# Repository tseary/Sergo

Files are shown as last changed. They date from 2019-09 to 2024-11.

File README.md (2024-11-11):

# Sergo
Sergo is a custom circuit board I made to interface hobby servos (or Geek servos) with Lego Power Functions. It has an ATTINY84 microcontroller and a 5 V, 2.5 A buck converter. It supports up to two servos, and can be controlled either from a PF receiver or directly by IR remote. It is programmed in Arduino.

54124418031_3b0a96d11d_c

# Make Your Own
Disclaimer: This is not a how-to guide. I have shared this project for general interest and in case the source code is useful to anyone. However, if you want to make your own Sergo, I am assuming you already have some knowledge of surface-mount soldering. You will need reflow soldering materials and equipment. **This project _cannot_ be assembled with only a soldering iron!**

## Gather Parts
The bare PCB without components can be ordered from [OSH Park](https://oshpark.com/shared_projects/rSyxp330).



Here is a [Digikey cart](https://www.digikey.ca/short/tn3525p4) with all of the components. The cost of parts for one board is about $15.61 CAD (or $13.92 CAD if the IR receiver is omitted).

It is recommended to apply solder paste to the board with a stencil. I used a polyimide film stencil of 0.005" thickness from [OSH Stencils](https://www.oshstencils.com). The stencil gerber file is "KiCad/gerbers/Sergo-F_Paste.gbr". Alternatively, solder paste may be applied freehand with a syringe. Particular care should be taken to apply the paste neatly under the buck converter PS1.

## Assembly, Programming, and Testing
More details to come...

# Show Me!
If you do attempt to build this project, I'd like to see it! Find me on [Eurobricks](https://www.eurobricks.com/forum/index.php?/profile/207750-tseary/).

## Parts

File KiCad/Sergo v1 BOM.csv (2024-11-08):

Id | Designator | Package | Quantity | Designation | Supplier and ref
1 | C1 | 1206 | 1 | 47uF
2 | C4,C5,C3 | 0805 | 3 | 0.1uF
3 | P2 | Pin_Header_02x03 | 1 | ICSP
4 | P3 | Pin_Header_02x03 | 1 | SERVOS
5 | U2 | TSOP382_RA | 1 | TSOP38238
6 | C2 | C_SMT_D8 | 1 | 220uF 10V
7 | R2,R3 | 0805 | 2 | 10k
8 | R4 | 0805 | 1 | 33
9 | PS1 | DC-DC_MYLSM00502ERPL | 1 | MYLSM00502ERPL
10 | P1 | Conn_Micro-MaTch_215570-4 | 1 | POWER FUNCTIONS
11 | F1 | 1812 | 1 | 1.5A
12 | D1 | SOT-23_Diode_ANK | 1 | 15V
13 | D2 | SOT-23 | 1 | ZENER 4.3V
14 | U1 | SOIC-14 | 1 | ATTINY84-S
15 | R1 | 0805 | 1 | 1k
16 | JP2 | 0805_JUMPER | 1 | CH2
17 | JP1 | 0805_JUMPER | 1 | CH1

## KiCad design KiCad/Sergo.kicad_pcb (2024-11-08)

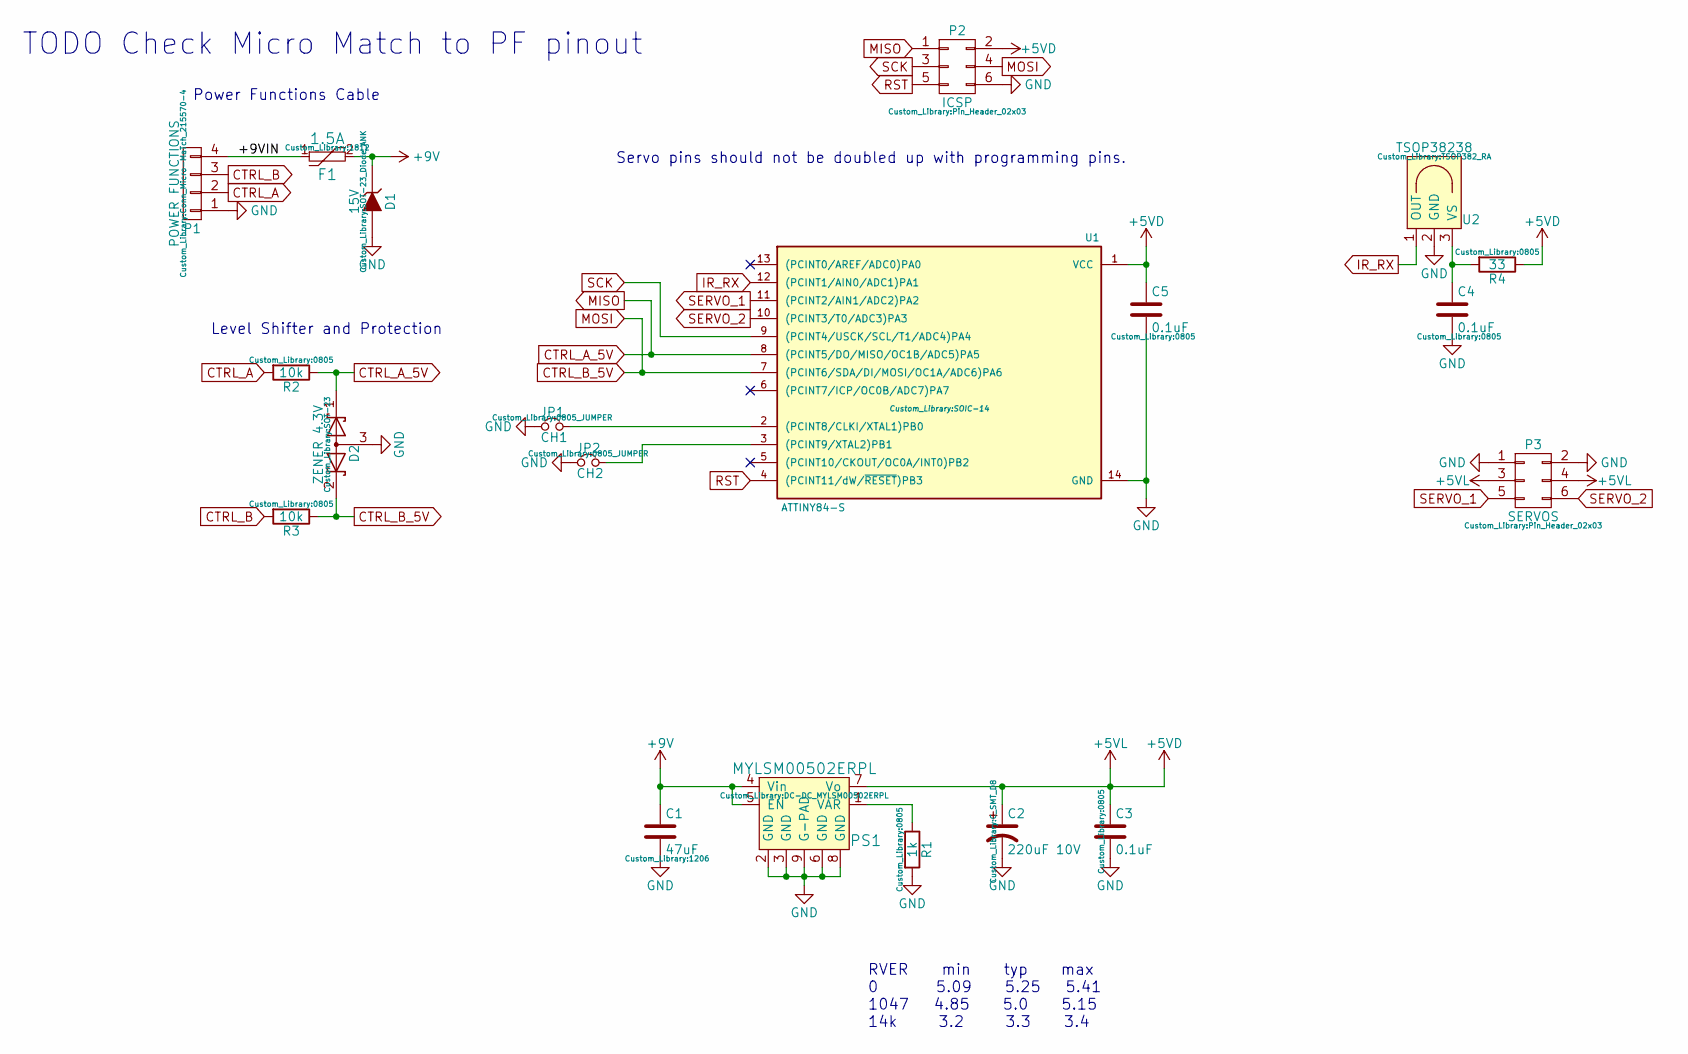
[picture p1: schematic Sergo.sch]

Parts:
C1: 47uF; 1206
C2: 220uF 10V; C_SMT_D8
C3, C4, C5: 0.1uF; 0805
D1: 15V; SOT-23_Diode_ANK
D2: ZENER 4.3V; SOT-23
F1: 1.5A; 1812
JP1: CH1; 0805_JUMPER
JP2: CH2; 0805_JUMPER
P1: POWER FUNCTIONS; Conn_Micro-MaTch_215570-4
P2: ICSP; Pin_Header_02x03
P3: SERVOS; Pin_Header_02x03
PS1: MYLSM00502ERPL; DC-DC_MYLSM00502ERPL
R1: 1k; 0805
R2, R3: 10k; 0805
R4: 33; 0805
U1: ATTINY84-S; SOIC-14
U2: TSOP38238; TSOP382_RA

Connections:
+5VD: C2.1, C3.1, C5.1, P2.2, P3.3, P3.4, PS1.7 (Vo), R4.1, U1.1 (VCC)
+9V: C1.1, D1.1 (K), F1.2, PS1.4 (Vin), PS1.5 (EN)
/+9VIN: F1.1, P1.4
CTRL_A: P1.2, R2.2
CTRL_B: P1.3, R3.2
CTRL_B_5V: D2.2 (K), P2.4, R3.1, U1.7 ((PCINT6/SDA/DI/MOSI/OC1A/ADC6)PA6)
GND: C1.2, C2.2, C3.2, C4.2, C5.2, D1.2 (A), D2.3 (A), JP1.1, JP2.1, P1.1, P2.6, P3.1, P3.2, PS1.2 (GND), PS1.3 (GND), PS1.6 (GND), PS1.8 (GND), PS1.9 (G-PAD), R1.2, U1.14 (GND), U2.2 (GND)
IR_RX: U1.12 ((PCINT1/AIN0/ADC1)PA1), U2.1 (OUT)
MISO: D2.1 (K), P2.1, R2.1, U1.8 ((PCINT5/DO/MISO/OC1B/ADC5)PA5)
unnamed: C4.1, R4.2, U2.3 (VS)
unnamed: JP1.2, U1.2 ((PCINT8/CLKI/XTAL1)PB0)
unnamed: JP2.2, U1.3 ((PCINT9/XTAL2)PB1)
unnamed: PS1.1 (VAR), R1.1
RST: P2.5, U1.4 ((PCINT11/dW/~RESET~)PB3)
SCK: P2.3, U1.9 ((PCINT4/USCK/SCL/T1/ADC4)PA4)
SERVO_1: P3.5, U1.11 ((PCINT2/AIN1/ADC2)PA2)
SERVO_2: P3.6, U1.10 ((PCINT3/T0/ADC3)PA3)

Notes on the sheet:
RVER min typ max 0 5.09 5.25 5.41 1047 4.85 5.0 5.15 14k 3.2 3.3 3.4
Level Shifter and Protection
Power Functions Cable
Servo pins should not be doubled up with programming pins.
TODO Check Micro Match to PF pinout

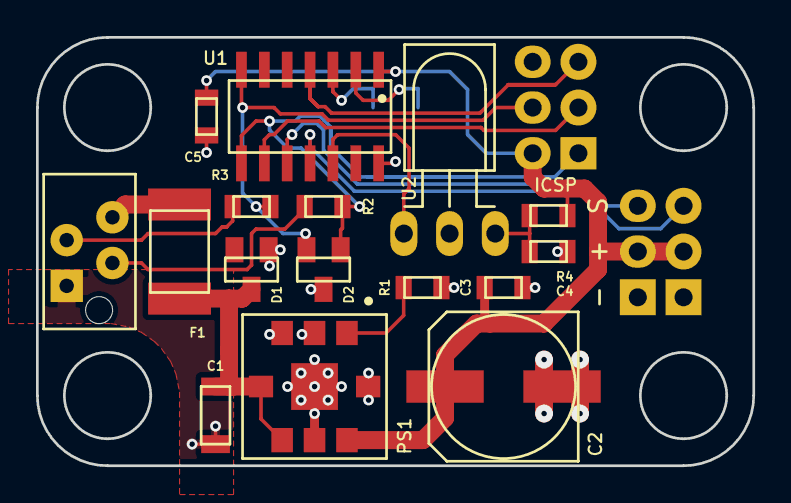
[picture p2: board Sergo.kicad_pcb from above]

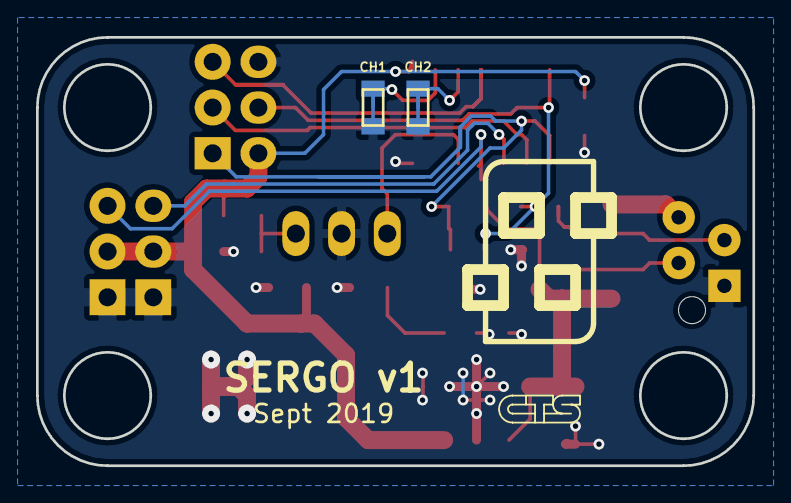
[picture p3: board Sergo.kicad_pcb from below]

Board: 2 copper layers, 39.8 x 23.8 mm, 20 parts (2 on the bottom side), 17 nets.

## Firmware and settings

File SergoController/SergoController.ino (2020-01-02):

/*
	Name:       IR_Test_3.ino
	Created:	9/21/2019 10:29:40 AM
	Author:     SCROLLSAW\Thomas
*/

#include "SoftServoLowLatency.h"

// IR Receiver
const uint8_t IR_RX_PIN = 1;	// Arduino pin 2 on ATTINY84 is PCINT2

// Channel selection pins
const uint8_t
CH1_INPUT_PIN = 10,
CH2_INPUT_PIN = 9;

// Control inputs
const uint8_t
C1_INPUT_PIN = 5,	// TODO check schematic
C2_INPUT_PIN = 6;

bool nextC1, nextC2, lastC1, lastC2;

// Channel and address space
uint8_t myChannelAddress;	// [0-3] << 1

// Message receiving
const uint8_t MESSAGE_LENGTH = 16;
volatile uint32_t
lastMicros = 0,
pulseLength = 0;
// The MSB is the first bit received
volatile uint16_t volMessage = 0x0000;
volatile uint8_t volMessageLength = 0;
volatile bool messageReady = false;

// Message parsing
bool lastToggleBit = false;
const bool verifyToggleBit = false;	// Ignore the toggle bit

/*const uint8_t
MODE_NOT_USED = 0b000,
MODE_COMBO_DIRECT = 0b001,
MODE_SINGLE_PIN_CONTINUOUS = 0b010,
MODE_SINGLE_PIN_TIMEOUT = 0b010,
MODE_SINGLE_OUTPUT_PWM_A = 0b100,
MODE_SINGLE_OUTPUT_PWM_B = 0b101,
MODE_SINGLE_OUTPUT_CST_A = 0b110,
MODE_SINGLE_OUTPUT_CST_B = 0b100;*/

const uint8_t
COMBO_DIRECT_FLOAT = 0b00,
COMBO_DIRECT_FWD = 0b01,
COMBO_DIRECT_REV = 0b10,
COMBO_DIRECT_BRAKE = 0b11;

// Servos
SoftServoLowLatency servoA, servoB;
const uint8_t SERVO_A_PIN = 2, SERVO_B_PIN = 3;
const int POS_CENTER = 90, POS_SWING = 20;
bool pulseOnEither = false;
uint32_t refreshTime = 0;

// Timeout
const uint32_t TIMEOUT_MILLIS = 2000;
uint32_t lastCommandMillis = 0;
bool doTimeout = false;

void setup() {
	// C1 and C2 input pins
	setupControl();

	// Set up servos
	servoA.attach(SERVO_A_PIN);
	servoA.write(POS_CENTER);
	servoB.attach(SERVO_B_PIN);
	servoB.write(POS_CENTER);

	// Set up pin change interrupts on RX
	setupChannel();
	pinMode(IR_RX_PIN, INPUT);
	GIMSK |= bit(PCIE0);	// turns on pin change interrupts
	PCMSK0 |= bit(PCINT1);	// turn on interrupts on RX pin

	// Turn on interrupts
	sei();
}

// Channel change becomes effective after reset
void setupChannel() {
	pinMode(CH1_INPUT_PIN, INPUT_PULLUP);
	pinMode(CH2_INPUT_PIN, INPUT_PULLUP);

	// Read channel
	myChannelAddress = (!digitalRead(CH1_INPUT_PIN) ? 0b010 : 0) +
		(!digitalRead(CH2_INPUT_PIN) ? 0b100 : 0);

	// Let pins float
	pinMode(CH1_INPUT_PIN, INPUT);
	pinMode(CH2_INPUT_PIN, INPUT);
}

void setupControl() {
	pinMode(C1_INPUT_PIN, INPUT_PULLUP);
	pinMode(C2_INPUT_PIN, INPUT_PULLUP);

	// Flush the values of lastC1 and lastC2
	readControl();
}

void loop() {
	checkMessage();
	checkTimeout();

	updateControl();

	refreshServos();
}

void checkMessage() {
	if (!messageReady) return;

	// Make a copy of the volatile variable
	cli();
	messageReady = false;
	uint16_t message = volMessage;
	sei();

	/**************************************************************************
	* Message Parsing
	*
	* The message structure is 16 bits:
	* TECC aMMM DDDD LLLL
	*
	* T    - toggles for every new command
	* E    - 0 = use MMM below to determine mode
	*        1 = Combo PWM mode (timeout)
	* CC   - Channel 0 to 3
	* a    - 0 = RC receiver address space
	*        1 = extra address space
	* MMM  - 000 = Not used in PF RC Receiver
	*        001 = Combo direct(timeout)
	*        010 = Single pin continuous(no timeout)
	*        011 = Single pin timeout
	*        1xx = Single output
	* DDDD - Data, meaning depends on mode
	* LLLL - Checksum, 0xf ^ nibble1 ^ nibble2 ^ nibble3
	***************************************************************************/

	// Channel is the most likely reason to reject a message, so check that first
	// Channel
	uint8_t channelAddress = (message >> 11) & 0b111;
	// Ignore if the message is for a different channel
	if (channelAddress != myChannelAddress) {
		return;
	}

	// Checksum
	uint16_t checksum = ~((message >> 12) ^
		(message >> 8) ^ (message >> 4)) & 0x0f;
	bool correct = (message & 0x0f) == checksum;
	// Fail if the checksum is wrong
	if (!correct) {
		return;
	}

	// Toggle bit
	if (verifyToggleBit) {
		bool toggleBit = (message >> 15) & 1;
		// Ignore if the toggle bit is the same as previously
		if (toggleBit == lastToggleBit) {
			return;
		}
		lastToggleBit = toggleBit;
	}

	// Mode and data
	uint8_t mode = (message >> 8) & 0b111,
		data = (message >> 4) & 0b1111;
	switch (mode) {
	case 0b000:	// Not used in PF RC receiver
		break;
	case 0b001:	// Combo direct (timeout)
		comboDirect(data);
		break;
	case 0b010:	// Single pin continuous
		singlePinContinuous(data);
		break;
	case 0b011:	// Single pin timeout
		singlePinTimeout(data);
		break;
	default: // Single output
		singleOutput(data);
		break;
	}
}

/*******************************************************************************
* Power Functions pin control
*******************************************************************************/

// TODO use inline for all update functions in main loop
void updateControl() {
	// Read the control pins
	readControl();

	// Do nothing if the control hasn't changed
	if (nextC1 == lastC1 && nextC2 == lastC2) return;

	// Execute control command
	uint16_t position = POS_CENTER;
	if (nextC1 && !nextC2) {
		// Forward
		position += POS_SWING;
	} else if (!nextC1 && nextC2) {
		// Reverse
		position -= POS_SWING;
	}
	servoA.write(position);
	servoB.write(position);
}

inline void readControl() {
	// Read the control pins
	lastC1 = nextC1;
	lastC2 = nextC2;
	nextC1 = digitalRead(C1_INPUT_PIN);
	nextC2 = digitalRead(C2_INPUT_PIN);
}

/*******************************************************************************
* Power Functions modes
*******************************************************************************/

void comboDirect(uint8_t data) {
	uint8_t motorACode = data & 0b11;
	uint16_t positionA = POS_CENTER;
	switch (motorACode) {
	case COMBO_DIRECT_FWD:
		positionA += POS_SWING;
		break;
	case COMBO_DIRECT_REV:
		positionA -= POS_SWING;
		break;
	}
	servoA.write(positionA);

	uint8_t motorBCode = (data >> 2) & 0b11;
	uint16_t positionB = POS_CENTER;
	switch (motorBCode) {
	case COMBO_DIRECT_FWD:
		positionB += POS_SWING;
		break;
	case COMBO_DIRECT_REV:
		positionB -= POS_SWING;
		break;
	}
	servoB.write(positionB);

	startTimeout();
}

void singlePinContinuous(uint8_t data) {

}

void singlePinTimeout(uint8_t data) {

}

void singleOutput(uint8_t data) {

}

/*******************************************************************************
* Timeout
*******************************************************************************/

void checkTimeout() {
	if (!doTimeout) return;
	if ((millis() - lastCommandMillis) >= TIMEOUT_MILLIS) {
		floatMotors();
		doTimeout = false;
	}
}

void startTimeout() {
	lastCommandMillis = millis();
	doTimeout = true;
}

void clearTimeout() {
	doTimeout = false;
}

/*******************************************************************************
* Low-Level motor commands
*******************************************************************************/

void floatMotors() {
	// DEBUG
	servoA.write(POS_CENTER);
	servoB.write(POS_CENTER);
}

void refreshServos() {
	if (pulseOnEither) {
		pulseOnEither = servoA.refresh();
		pulseOnEither |= servoB.refresh();
	} else if (millis() >= refreshTime) {
		pulseOnEither = servoA.refresh();
		pulseOnEither |= servoB.refresh();
		refreshTime += 20;
	}
}

/*******************************************************************************
* Interrupts
*******************************************************************************/

ISR(PCINT0_vect) {
	// Ignore rising edges (end of IR mark)
	if (digitalRead(IR_RX_PIN)) {
		return;
	}

	uint32_t microsNow = micros();
	pulseLength = microsNow - lastMicros;

	if (pulseLength < 316) {
		// Invalid, ignore
		return;
	} else if (pulseLength < 526) {
		// Low bit
		volMessageLength++;
	} else if (pulseLength < 947) {
		// High bit
		volMessage |= 1 << (MESSAGE_LENGTH - ++volMessageLength);
	} else {
		// Start bit
		// If pulseLength < 1579, this might be a stop bit for the first of two back-to-back messages.
		volMessage = 0;
		volMessageLength = 0;
	}

	lastMicros = microsNow;
	messageReady = volMessageLength == MESSAGE_LENGTH;
}

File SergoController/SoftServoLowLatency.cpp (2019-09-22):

// This is an ultra simple software servo driver. For best
// results, use with a timer0 interrupt to refresh() all
// your servos once every 20 milliseconds!
// Written by Limor Fried for Adafruit Industries, BSD license

#if ARDUINO >= 100
#include "Arduino.h"
#else
#include "WProgram.h"
#endif

#include "SoftServoLowLatency.h"

SoftServoLowLatency::SoftServoLowLatency(uint16_t maxLatency) {
	_maxLatency = maxLatency;
}

void SoftServoLowLatency::attach(uint8_t pin) {
	servoPin = pin;
	angle = 90;
	isAttached = true;
	pinMode(servoPin, OUTPUT);
}

void SoftServoLowLatency::detach(void) {
	isAttached = false;
	pinMode(servoPin, INPUT);
}

boolean  SoftServoLowLatency::attached(void) {
	return isAttached;
}

void SoftServoLowLatency::write(uint8_t degrees) {
	angle = degrees;
	if (!isAttached) return;
	pulseMicros = map(degrees, 0, 180, 1000, 2000);
}

bool SoftServoLowLatency::refresh(void) {

	// TODO Maybe pause interrupts during this entire function
	cli();

	// If pulseMicros changes during a pulse,
	// the change takes effect on the next pulse.

	if (pulseOn) {
		// We are partway through a pulse
		// Check the remainging time
		int remaining = pulseEndMicros - micros();
		if (remaining <= 0) {
			// Pulse end is overdue, so end it immediately
			digitalWrite(servoPin, pulseOn = false);
		} else if (remaining <= _maxLatency) {
			// Pulse end is soon, so pause interrupts and finish it now
			//cli();
			delayMicroseconds(remaining);
			digitalWrite(servoPin, pulseOn = false);
			//sei();
		}
	} else {
		// A pulse hasn't been started
		if (millis() >= pulseStartMillis) {
			// Time to start
			digitalWrite(servoPin, pulseOn = true);
			pulseEndMicros = micros() + pulseMicros;
			pulseStartMillis += PULSE_PERIOD_MILLIS;
		}
	}

	sei();
	return pulseOn;
}

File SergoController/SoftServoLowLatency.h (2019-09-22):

// This is an ultra simple software servo driver. For best
// results, use with a timer0 interrupt to refresh() all
// your servos once every 20 milliseconds!
// Written by Limor Fried for Adafruit Industries, BSD license

// Modified by Thomas Seary, Sept 2019

#pragma once

#if ARDUINO >= 100
#include "Arduino.h"
#else
#include "WProgram.h"
#endif

class SoftServoLowLatency {
public:
	// Lower maxLatency allows more time-sensitive tasks outside of this class.
	// Higher maxLatency may improve servo accuracy. Default is 250 us.
	SoftServoLowLatency(uint16_t maxLatency = 250);
	void attach(uint8_t pin);
	void detach();
	boolean attached();
	void write(uint8_t degrees);

	// Returns true if a pulse is active.
	// If it returns true, refresh() should be called continuously.
	// If it returns false, the next call should be made within 20 milliseconds.
	bool refresh(void);
private:
	bool isAttached = false;
	uint8_t servoPin = 255;	// The digital pin number
	uint8_t angle = 90;		// Servo angle in degrees
	uint16_t pulseMicros;	// The length of the pulse in microseconds

	bool pulseOn = false;
	uint32_t pulseStartMillis = 0;	// The time in millis to start the next pulse
	uint32_t pulseEndMicros = 0;	// The time in micros to end the current pulse
	uint16_t _maxLatency = 200;
	static const uint16_t PULSE_PERIOD_MILLIS = 20;
};

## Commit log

2019-09-21 Added test code for ATMEGA328P
    Proof of concept, receiving PF IR commands and controlling a servo.
2019-09-22 Adjusted servo center
2019-09-22 Port from ATMEGA328P to ATTINY84
    Removed 328-specific functionality. Updated interrupts for ATTINY84. Now using modified SoftServo library instead of normal Servo library.
2019-09-22 Second servo
    Added second servo and changed servo pin numbers. Fixed lost communication timeout.
    [SergoController.ino, SoftServoLowLatency.cpp]
2019-09-25 Swap pins
    Swapped RX and servo B pins to improve PCB layout.
    [SergoController.ino]
2024-11-08 Add KiCad project
    Here is the KiCad project for the PCB, as ordered.
    [Sergo v1 BOM.csv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]
